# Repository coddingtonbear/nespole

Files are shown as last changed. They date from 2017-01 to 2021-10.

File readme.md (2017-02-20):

# Microcontroller-controlled Laminator (Nespole)



Need to control your laminator's temperature precisely because you use it
for performing temperature-specific things like applying photosensitive
dry film to PCBs or trying out the toner transfer method?  This lets you
do that.

## Parts

* [AmazonBasics Thermal Laminator](https://www.amazon.com/AmazonBasics-PL9-US-Thermal-Laminator/dp/B00BUI5QWS); ~$21 as of this writing.
* 120VAC to 5VDC transformer; ~$5
* [MAX6675 and K-Type thermocouple](https://www.amazon.com/HiLetgo-MAX6675-Thermocouple-Temperature-Arduino/dp/B01HT871SO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);
  ~$5 -- you'll need to remove the chip and mounting pins from the little PCB for attaching to the final board.
* ATMega328pb microcontroller; ~$2 -- an ATMega328p would probably work just as well, but you may need to double-check the pinouts.
* Common-cathode 4-digit 7-segment (+decimal point) Display; ~$1
* AS1108WL common-cathode LED array controller or equivalent; ~$4
* PEC11S Rotary encoder w/ button; ~$3
* CH340G USB-Serial UART adapter; ~$1 -- not strictly necessary if you're comfortable programming the chip via the SPI bus
* CLX6A 3.5mm x 3.5mm RGB LED; &lt;$1
* A relay (for turning the heating element on/off)
* A variety of passives, a diode, a logic-level p-channel mosfet, a logic-level n-channel mosfet (all SOT-23), etc; see the schematic for details.

## Interface

Just turn the rotary encoder to set the target temperature; when you've found
your target temperature, press the rotary in to activate its button.  That's all.

There's a single RGB LED on-board; various LED colors mean various things
including:

* Off: The heating element is off.
* Blue: The unit is starting up.
* White: You are setting the temperature right now.
* Red: The heating element is on.

## Schematics



The included schematics and layout are both correct (as far as I know), but
if you observe the photos linked here, you'll see that they differ in slight
ways.  If you look carefully, you'll see that I've had to correct several
oversights by using bodge wires or, in two cases, installing capacitors that
I neglected to include in the original design.  The attached schematic has,
though, been corrected to account for these oversights.

In case you're curious about the errors I made, they were the following:

* Added the bypass capacitors to the wrong pins of the microcontroller.  I
  did not notice this problem until very late in the game when I was trying
  to diagnose what was causing some erratic behavior.  The root cause of this
  was that I did not pay close-enough attention to which pin was the ADC's
  VCC and which pin was the microcontroller's normal VCC.  Really, though,
  there should be bypass capacitors for both, so I've updated the design
  to include them for both VCCs.
* Neglected to connect the CH340G's GND pin to anything at all.
* Mis-connected the N-Channel mosfet used for switching the laminator's
  relay.  I misread the datasheet and had swapped the source and drain
  pins.
* A couple traces were just a little too close together and had to be cut
  apart during various fabrication steps.

## Earlier Versions

### Nespole 1.0



The first version of nespole was intended to be just a bit simpler; it would
fetch measurements from a thermocouple in a way very similar to what Nespole 2.0
does (except via a slightly-newer MAX31855).  I encountered a ton of trouble
getting the thermocouple chip to return reasonable data, and eventually gave
up and reprogrammed this board to just provide a USB interface for flipping
the relay on-and-off.

## Future Thoughts

There are a couple things I'd perhaps change in a later iteration:

* Spend more time tweaking the layout so I can get the relay control header
  near the top of the board instead of the bottom.  This is something that
  could probably be done without a huge amount of further effort, but
  sometimes it's important to settle for "good enough".
* Place the alignment points off of the final board area instead of within
  it.  When making this board, I was using copper clad that was only very
  slightly larger than the final size and decided to be a little conservative.
* In the end, I used 5566 bytes of flash and only 300 bytes of memory; I could
  probably get by with a lower-powered microcontroller.  It's a little hard to
  beat the price of the ATMega328pb, though, so that might be more of a
  challenge than it is actually worth.

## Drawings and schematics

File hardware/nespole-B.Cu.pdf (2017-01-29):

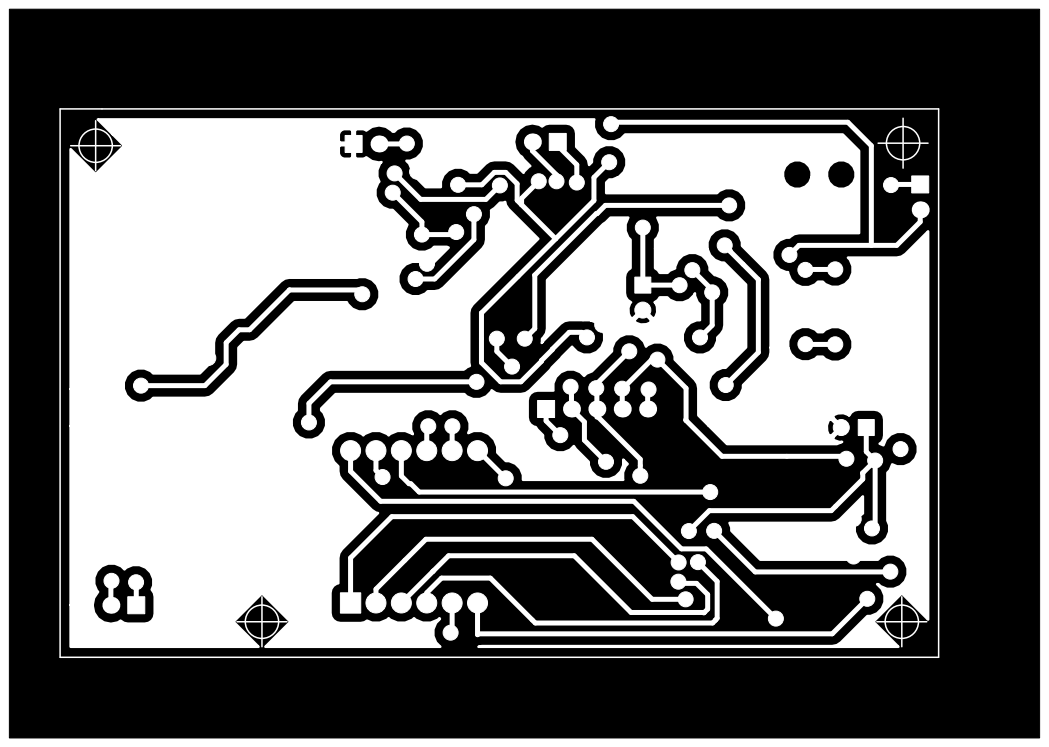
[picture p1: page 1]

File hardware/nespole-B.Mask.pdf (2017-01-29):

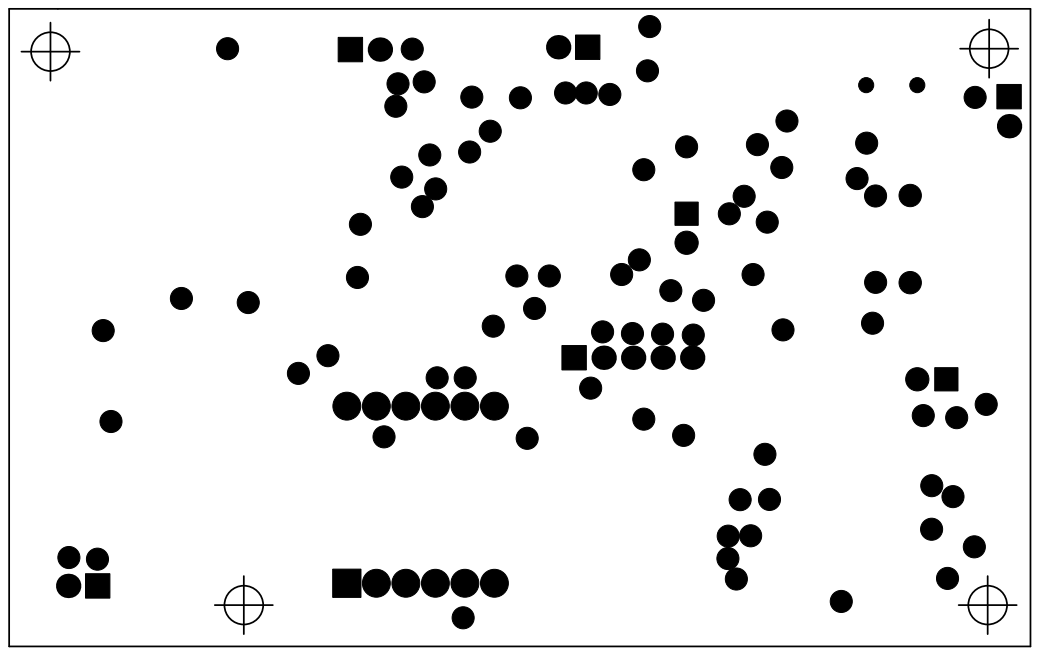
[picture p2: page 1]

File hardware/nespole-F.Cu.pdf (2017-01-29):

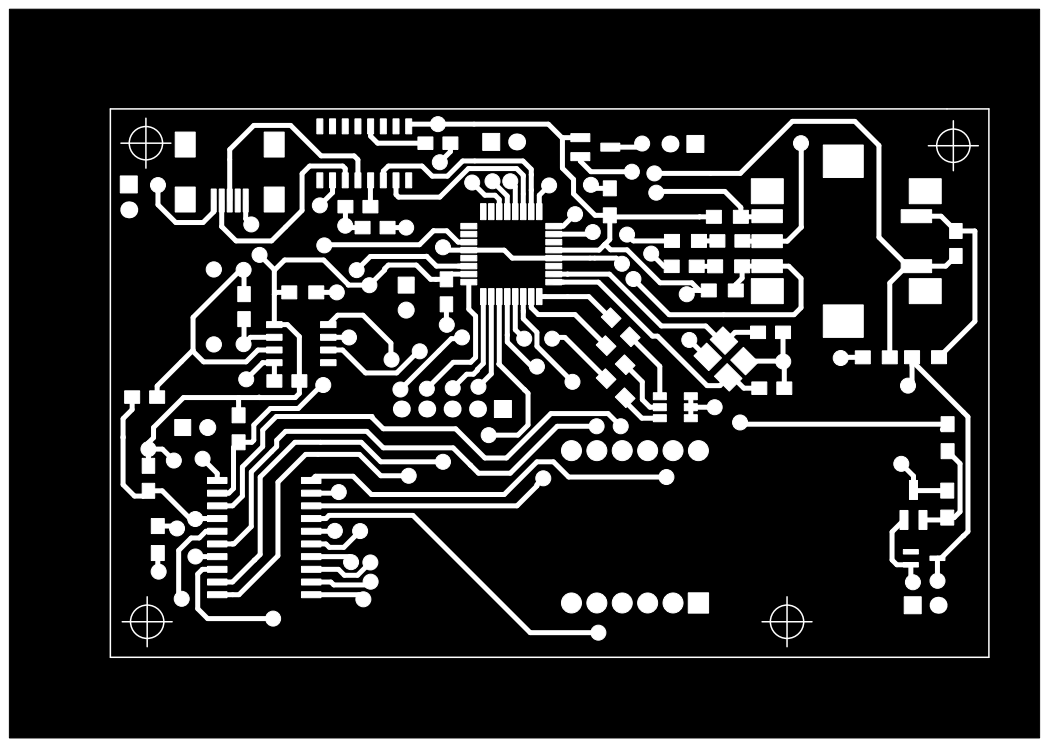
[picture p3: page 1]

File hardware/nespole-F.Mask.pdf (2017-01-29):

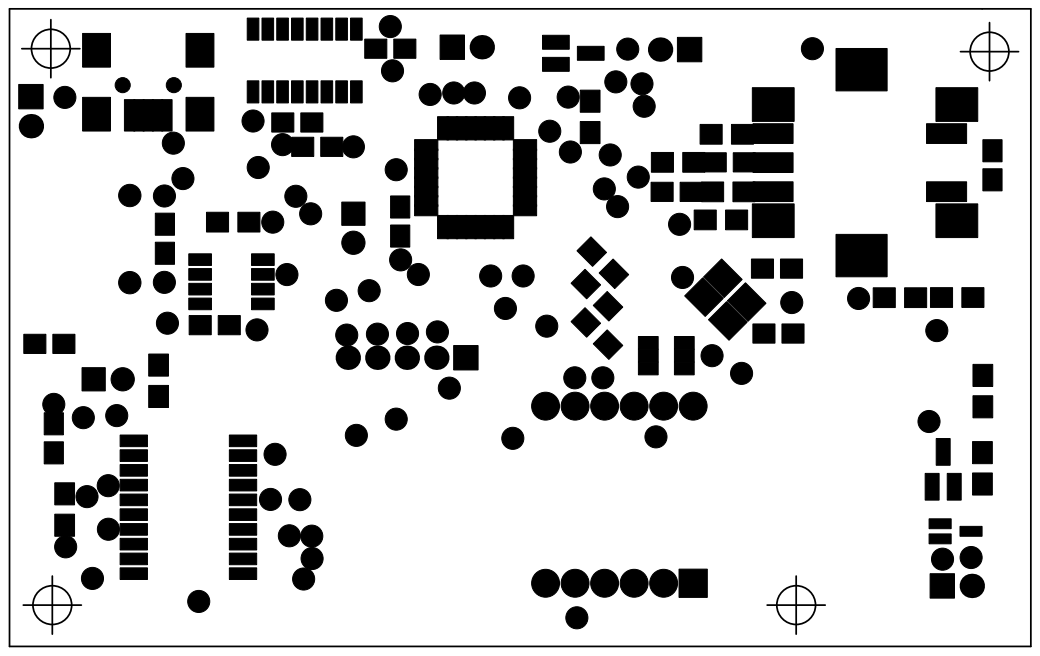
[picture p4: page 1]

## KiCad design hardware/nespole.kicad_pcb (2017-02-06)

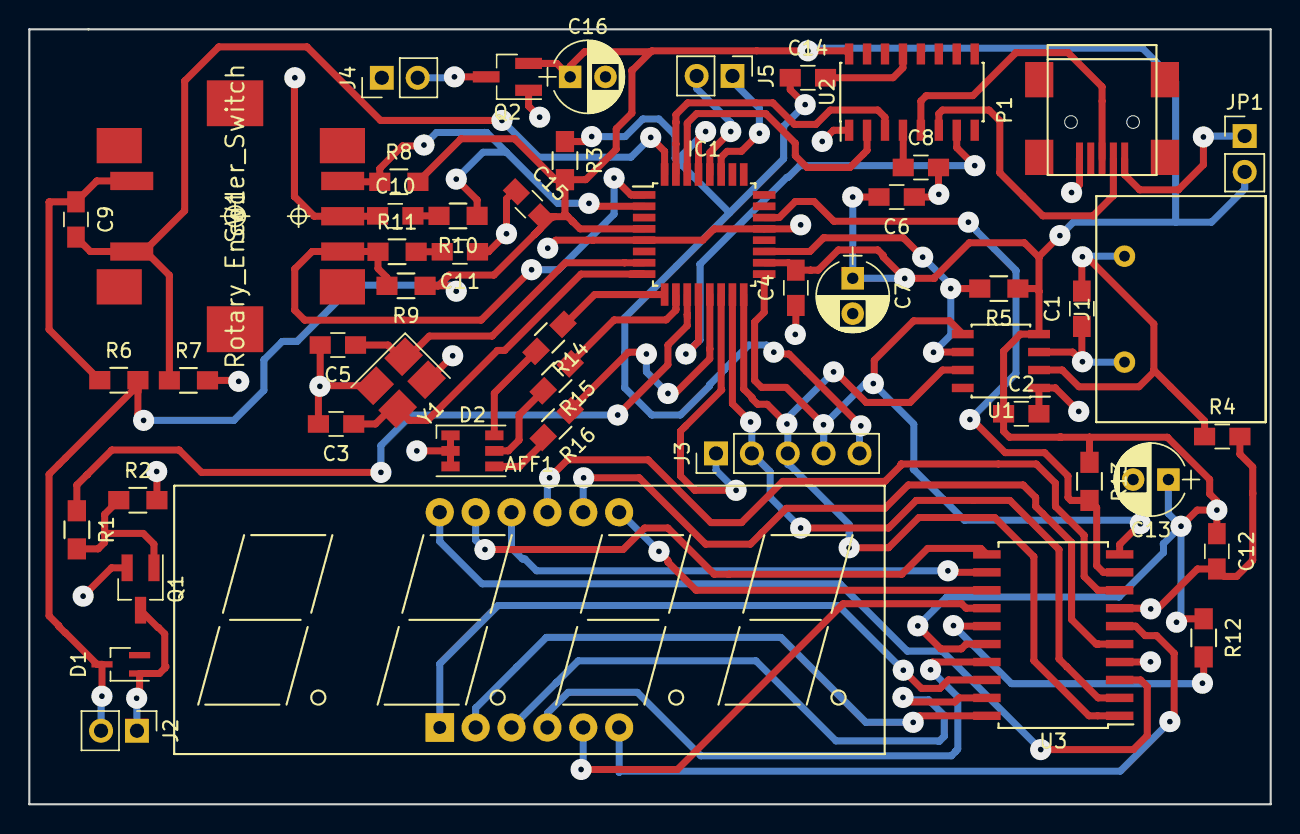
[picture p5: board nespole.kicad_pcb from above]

Board: 2 copper layers, 87.9 x 54.9 mm, 50 parts (0 on the bottom side), 52 nets.

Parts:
AFF1: CA56-12; Cx56-12
C1, C2, C4, C6, C8, C9, C10, C11, C14, C15: 0.1u; C_0805_HandSoldering
C3, C5: 22p; C_0805_HandSoldering
C7: 10m; CP_Radial_D5.0mm_P2.50mm
C12: 0.1uF; C_0805_HandSoldering
C13: 10u; CP_Radial_D5.0mm_P2.50mm
C16: 22m; CP_Radial_D5.0mm_P2.50mm
D1: D; SOT-323_DIODE
D2: LED_RGB; LED_RGB_PLCC-6
IC1: ATMEGA328PB-A; TQFP-32_7x7mm_Pitch0.8mm
J1: Screw_Terminal_1x02; 01x02_7.5mm_Header_Screw_Terminal
J2, J4, J5: Screw_Terminal_1x02; Pin_Header_Straight_1x02_Pitch2.54mm
J3: Screw_Terminal_1x05; Pin_Header_Straight_1x05_Pitch2.54mm
JP1: Jumper_NO_Small; Pin_Header_Straight_1x02_Pitch2.54mm
P1: USB_OTG; USB_Mini-B
Q1: MOSFET_N_CH; SOT-23_Handsoldering
Q2: MOSFET_P_CH; SOT-23_Handsoldering
R1: 270; R_0805_HandSoldering
R2, R3, R5, R7, R8, R9, R13: 10k; R_0805_HandSoldering
R4: 0; C_0805_HandSoldering
R6, R14, R15: 1k; R_0805_HandSoldering
R10, R11: 2.2k; R_0805_HandSoldering
R12: 9.53k; R_0805_HandSoldering
R16: 1.5k; R_0805_HandSoldering
SW1: Rotary_Encoder_Switch; ROTARY-ENCODER-PEC11S
U1: MAX6675; SOIC-8_3.9x4.9mm_Pitch1.27mm
U2: CH340G; SOIC-16_3.9x9.9mm_Pitch1.27mm
U3: AS1108; SOIC-20W_7.5x12.8mm_Pitch1.27mm
Y1: Crystal_GND24; Crystal_SMD_TXC_7M-4pin_3.2x2.5mm_HandSoldering

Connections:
+5V: C2.1, C4.2, C6.2, C7.1, C12.1, C13.1, C15.2, C16.1, D1.1, IC1.4, IC1.18, J2.2, JP1.2, Q2.S, R3.2, R5.1, R6.2, R8.2, R9.1, R12.1, R13.1, U1.4, U2.16, U3.16
/LED_DIGIT_0: AFF1.12, U3.3
/LED_DIGIT_1: AFF1.9, U3.8
/LED_DIGIT_2: AFF1.8, U3.5
/LED_DIGIT_3: AFF1.6, U3.6
/LED_SEGMENT_A: AFF1.11, U3.11
/LED_SEGMENT_B: AFF1.7, U3.13
/LED_SEGMENT_C: AFF1.4, U3.17
/LED_SEGMENT_D: AFF1.2, U3.20
/LED_SEGMENT_DP: AFF1.3, U3.19
/LED_SEGMENT_E: AFF1.1, U3.18
/LED_SEGMENT_F: AFF1.10, U3.12
/LED_SEGMENT_G: AFF1.5, U3.14
/to_relay: D1.2, J2.1, Q1.D
CLKOUT: IC1.12, U2.7
ENABLE_RELAY: IC1.11, R1.1
GND: C2.2, C3.2, C4.1, C5.2, C6.1, C7.2, C8.2, C10.1, C11.1, C12.2, C13.2, C15.1, C16.2, D2.1, D2.2, D2.3, IC1.5, IC1.21, J4.1, P1.5, Q1.S, Q2.G, R2.2, R4.2, R7.2, SW1.2, U1.1, U2.1, U3.4, U3.7, Y1.2, Y1.4
LED_B: IC1.9, R14.1
LED_CS: IC1.22, R13.2, U3.9
LED_G: IC1.10, R15.1
LED_R: IC1.13, R16.1
MC_CS: IC1.14, J3.1
MISO: IC1.16, J3.3, U1.7, U3.1
MOSI: IC1.15, J3.2, U3.2
unnamed: C1.1, J1.1, U1.3
unnamed: C1.2, J1.2, R4.1, U1.2
unnamed: C3.1, IC1.8, Y1.3
unnamed: C5.1, IC1.7, Y1.1
unnamed: C8.1, U2.4
unnamed: C9.1, R6.1, SW1.5
unnamed: C10.2, R10.2
unnamed: C11.2, R11.2
unnamed: C14.2, U2.13
unnamed: D2.4, R16.2
unnamed: D2.5, R15.2
unnamed: D2.6, R14.2
unnamed: J4.2, Q2.D
unnamed: JP1.1, P1.1
unnamed: P1.2, U2.6
unnamed: P1.3, U2.5
unnamed: Q1.G, R1.2, R2.1
unnamed: R12.2, U3.15
RESET: C14.1, IC1.29, J3.5, R3.1
RXD: IC1.30, U2.2
SCK: IC1.17, J3.4, U1.5, U3.10
SCL: IC1.28, J5.2
SDA: IC1.27, J5.1
SW_BUTTON: C9.2, IC1.32, R7.1, SW1.4
SW_DIR: IC1.2, R8.1, R10.1, SW1.3
SW_INT: IC1.1, R9.2, R11.1, SW1.1
TEMP_CS: IC1.19, R5.2, U1.6
TXD: IC1.31, U2.3

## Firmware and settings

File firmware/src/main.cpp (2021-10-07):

#include "main.h"

#define LED_R 9
#define LED_G 6
#define LED_B 5

#define SW_DIR 4
#define SW_INT 3
#define SW_BUTTON 2

#define CS_TEMP A6
#define CS_LED A7
#define CS_SELF 10

#define EN_RELAY 7

#define TARGET_EEPROM_ADDRESS 100

SPISettings slow(500000, MSBFIRST, SPI_MODE0);

#define SERIAL_TEMPERATURE_INTERVAL 100

unsigned long lastPrinted = 0;
volatile float currentTemperature = 0;
volatile float targetTemperature = 0;
volatile float allowRelay = false;
volatile float thermocoupleAttached = false;
bool relayEnabled = false;

volatile unsigned long showTargetUntil = 0;

int freeRam () {
    extern int __heap_start, *__brkval; 
    int v; 
    return (int) &v - (__brkval == 0 ? (int) &__heap_start : (int) __brkval); 
}


ISR(BADISR_vect)
{
    for (;;) UDR0='!';
}

void setup() {
    Serial.begin(9600);
    Serial.println("Nespole (2021-10-05)");
    if(MCUSR) {
        Serial.print("System restarted by reset: ");
        Serial.println(MCUSR, BIN);
        delay(30000);
    }
    MCUSR = 0;

    SPI.begin();
    pinMode(LED_R, OUTPUT);
    pinMode(LED_G, OUTPUT);
    pinMode(LED_B, OUTPUT);

    pinMode(SW_DIR, INPUT);
    pinMode(SW_INT, INPUT);
    pinMode(SW_BUTTON, INPUT);

    pinMode(CS_SELF, INPUT_PULLUP);
    pinMode(CS_TEMP, OUTPUT);
    pinMode(CS_LED, OUTPUT);
    pinMode(EN_RELAY, OUTPUT);

    digitalWrite(EN_RELAY, LOW);
    setLedColor(0, 0, 10);

    targetTemperature = EEPROM.read(TARGET_EEPROM_ADDRESS);
    if(targetTemperature > 200) { // The default is 255 if not prev stored.
        targetTemperature = 0;
    }

    attachInterrupt(digitalPinToInterrupt(SW_BUTTON), onButtonPressed, RISING);
    attachInterrupt(digitalPinToInterrupt(SW_INT), onEncoderTurned, RISING);

    setDisplayRegister(0x0c, 0 | (1 << 7) | (1 << 0)); // -Shutdown
    setDisplayRegister(0x09, 15); // Enable decoding for numbers
    setDisplayRegister(0x0a, 0); // Intensity
    setDisplayRegister(0x0e, 0 | (1 << 3)); // Features
    setDisplayRegister(0x0b, 3); // Display all four digits
}


void onButtonPressed() {
    cli();
    if(!allowRelay) {
        allowRelay = true;
    } else {
        allowRelay = false;
    }
    sei();
    return allowRelay;
}


void onEncoderTurned() {
    cli();
    if(digitalRead(SW_DIR) == LOW) {
        targetTemperature++;
    } else {
        targetTemperature--;
    }
    if (targetTemperature < 0) {
        targetTemperature = 0;
    }
    if (targetTemperature > 200) {
        targetTemperature = 200;
    }
    EEPROM.write(TARGET_EEPROM_ADDRESS, targetTemperature);
    showTargetUntil = millis() + 3000;
    sei();
}


float getTemperature() {
    SPI.beginTransaction(slow);
    digitalWrite(CS_TEMP, LOW);
    delayMicroseconds(10);

    uint16_t tempData;
    tempData = SPI.transfer(0xff) << 8;
    tempData |= SPI.transfer(0xff);

    thermocoupleAttached = true;
    if(tempData & 0x4) {
        thermocoupleAttached = false;
    }

    tempData >>=3;

    delayMicroseconds(10);
    digitalWrite(CS_TEMP, HIGH);
    SPI.endTransaction();

    return tempData * 0.25;
}


void setLedColor(uint8_t r, uint8_t g, uint8_t b) {
    analogWrite(LED_R, r);
    analogWrite(LED_G, g);
    analogWrite(LED_B, b);
}


void setDisplayRegister(byte registerId, byte value) {
    SPI.beginTransaction(slow);
    digitalWrite(CS_LED, LOW);
    delayMicroseconds(10);

    SPI.transfer(registerId);
    SPI.transfer(value);

    delayMicroseconds(10);
    digitalWrite(CS_LED, HIGH);
    SPI.endTransaction();
}


void setDisplayValue(float value) {
    int intValue = (int)(value * 10);

    uint8_t digit0 = (intValue % 10000) / 1000;
    uint8_t digit1 = (intValue % 1000) / 100;
    uint8_t digit2 = (intValue % 100) / 10;
    uint8_t digit3 = (intValue % 10);

    if(digit0) {
        setDisplayRegister(1, digit0);
    } else {
        setDisplayRegister(1, 0xf);
    }
    if(digit1 || digit0) {
        setDisplayRegister(2, digit1);
    } else {
        setDisplayRegister(2, 0xf);
    }
    setDisplayRegister(3, digit2 | (1 << 7));
    setDisplayRegister(4, digit3);
}


void enableRelay() {
    relayEnabled = true;
    setLedColor(10, 0, 0);
    digitalWrite(EN_RELAY, HIGH);
}

void disableRelay() {
    relayEnabled = false;
    setLedColor(0, 0, 0);
    digitalWrite(EN_RELAY, LOW);
}

char incomingText[100] = "\0";


void loop() {
    currentTemperature = getTemperature();
    if(millis() < showTargetUntil) {
        disableRelay();
        setLedColor(10, 10, 10);
        setDisplayValue(targetTemperature);
    } else {
        if(millis() - lastPrinted > SERIAL_TEMPERATURE_INTERVAL) {
            lastPrinted = millis();
            Serial.print("Current:\t");
            Serial.print(currentTemperature);
            Serial.print("\tTarget:\t");
            Serial.print(targetTemperature);
            if(allowRelay) {
                Serial.print("\t(enabled)");
            }
            if(relayEnabled) {
                Serial.print("\t(heating)");
            }
            if (!thermocoupleAttached) {
                Serial.print("\t(no thermocouple!)");
            }
            Serial.println();
        }
        if(Serial.available()) {
            char incomingChar = Serial.read();
            if(incomingChar == '\n') {
                if(strlen(incomingText) == 1) {
                    onButtonPressed();
                } else {
                    targetTemperature = atoi(incomingText);
                    Serial.print("Temperature set to ");
                    Serial.print(targetTemperature);
                    Serial.println(" by serial command.");
                    incomingText[0] = '\0';
                }
            } else {
                strncat(incomingText, &incomingChar, 1);
            }
        }

        if(
            (currentTemperature < targetTemperature) &&
            allowRelay &&
            thermocoupleAttached
        ) {
            setDisplayValue(currentTemperature);
            enableRelay();
        } else if(!thermocoupleAttached) {
            for(int i = 1; i<=4; i++) {
                setDisplayRegister(i, 10);
            }
            disableRelay();
        } else {
            setDisplayValue(currentTemperature);
            disableRelay();
        }
    }
    delay(250);
}

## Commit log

2017-01-02 And so it begins...
    [nespole.kicad_pcb, nespole.sch]
2017-01-03 First revision board renderings.
    [nespole.kicad_pcb, nespole.sch]
2017-01-04 Updating board to use mosfet for switching relay on/off.
    [nespole.kicad_pcb, nespole.sch]
2017-01-07 Updating hardware for latest version.
    [nespole.sch]
2017-01-08 Updating to use ATMEGA2313; I needed just one more pin :-(.
    [nespole.kicad_pcb, nespole.sch]
2017-01-08 Fixing a missing GND trace.
    [nespole.sch]
2017-01-09 Just drive the relay directly...this MAX31855 is just not working properly.
    [nespole.kicad_pcb]
2017-01-28 Updating hardware for new display.
    [nespole.kicad_pcb, nespole.sch]
2017-01-28 Slightly better layout.
    [nespole.dsn, nespole.kicad_pcb, nespole.sch]
2017-01-28 Cutting groundplane to size; adding edge cuts.
    [nespole.kicad_pcb]
2017-01-28 Adding a keepout area below the 12mhz crystal.
    [nespole.kicad_pcb]
2017-01-28 Minor layout changes; exposing I2C bus via header.
    [nespole.kicad_pcb, nespole.sch]
2017-01-28 Explicitly un-mark LED resistors.
    [nespole.kicad_pcb, nespole.sch]
2017-01-28 Whoops; neglected to press the PCB update button.
    [nespole.kicad_pcb]
2017-01-28 I'm glad I checked -- the CH341T has a slightly wider size from normal TSSOP-20s.
    [nespole.kicad_pcb]
2017-01-29 Updating netlist to use new CH341-specific footprint.
    [nespole.sch]
2017-01-29 Increase traces to 0.5mm; swap CH341T with CH340G; add USB power jumper.
    [nespole.kicad_pcb, nespole.sch]
2017-01-29 Better ground plane unity.
    [nespole.kicad_pcb]
2017-02-05 Updating hardware to correct for...mistakes; finishing-up software.
    [nespole.kicad_pcb, nespole.sch]
2017-02-06 Fully-working; fixed schematic to wire the mosfet properly.
    [nespole.kicad_pcb, nespole.sch]
2017-02-06 Clarifying why there are more capacitors.
2017-02-20 Adding schematic rendering.
